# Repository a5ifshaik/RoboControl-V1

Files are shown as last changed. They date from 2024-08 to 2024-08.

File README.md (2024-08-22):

# RoboControl V1 - Arduino-based Robot Control Board
<p align="justify"> The RoboControl is a cheap and beginner-friendly all-in-one robot control board which is capable of dual motor control (6A/Channel), and includes dedicated pinouts for servos, sensors and external 12V systems which is controlled using a MOSFET. It also features a built in battery level sensing circuit which is made up of a simple voltage divider that translates the 0-12V range of the input battery to a analog value range between 0-1023. </p>



## Features
- 12V - 24V Input Voltage
- Arduino Nano MCU
- Two Infineon IFX9201SG Motor Drivers (Supports up to 6A/driver)
- MOSFET for External Circuit Control
- Battery Voltage Monitor
- Dedicated ports for sensors/servos

## Pinout 
| On RCB | Arduino Pin | Description | 
| --- | --- |  --- |
| S1 | D6 | Servo 1 Port; comes with 5V and GND supply |
| S2 | D9 | Servo 2 Port; comes with 5V and GND supply |
| SCL | A5 | Serial Clock Line used for I2C | 
| SDA | A4 | Serial Data Line used for I2C | 
| BZOUT | D7 | MOSFET control line, 5V to turn on 12V line |
| TRIG | D12 | Trigger Pin for Ultrasonic Sensor (Can use as normal digital)  |
| ECHO | D11 | Echo Pin for Ultrasonic Sensor (Can use as normal digital) |
| BATT | A3 | Battery monitor pin, produces analog reading between 0 - 1023  |
| M1 PWM | D3 | PWM Signal supply pin for Motor 1 driver |
| M1 DIR | D8 | Motor 1 Direction Pin (1/0 for CW/CCW or vv) |
| M1 EN | D2 | Motor 1 Enable Pin, Set as HIGH to enable driver |
| M2 PWM | D5 | PWM Signal supply pin for Motor 2 driver |
| M2 DIR | D10 | Motor 2 Direction Pin (1/0 for CW/CCW or vv) |
| M2 EN | D4 | Motor 2 Enable Pin, Set as HIGH to enable driver |

## Schematics:


## 3D Render


## Sample Applications
### The RoboControl board was initially developed for a home-surveillance robot with 2 wheels, but can be used for various applications that have similar needs.



###### **In Image 2, the yellow jumpers are used to correct an error found post-production which has since been rectified in this repository.

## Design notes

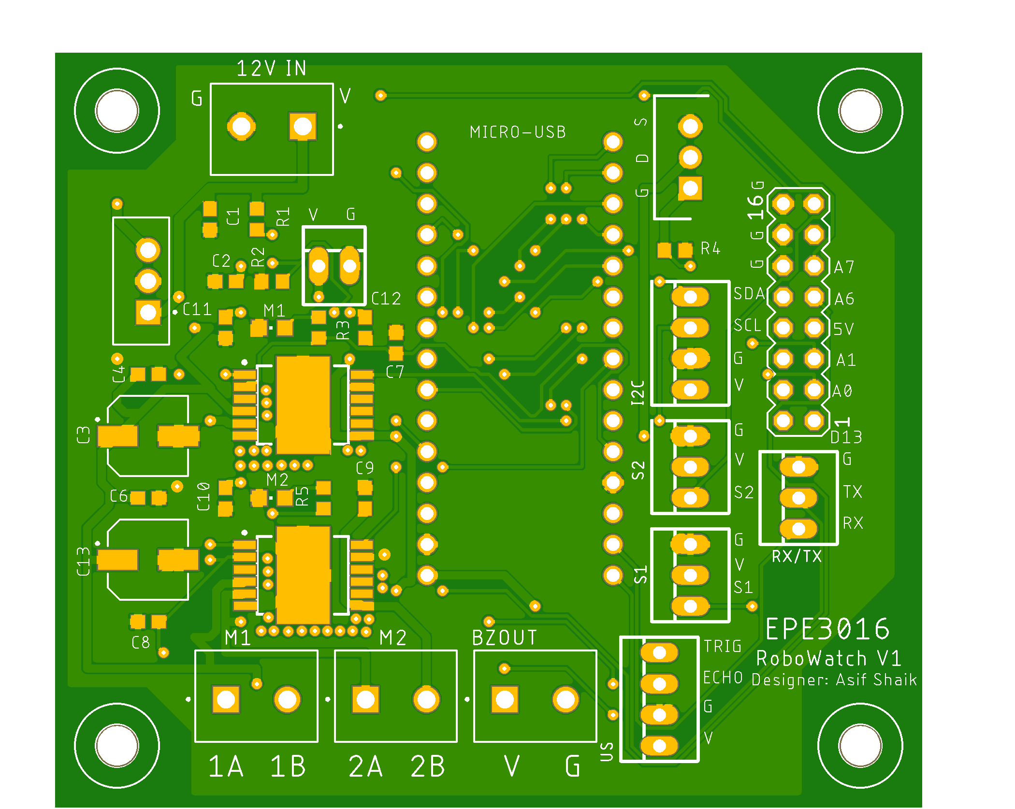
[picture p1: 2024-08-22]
3D Board Render.png

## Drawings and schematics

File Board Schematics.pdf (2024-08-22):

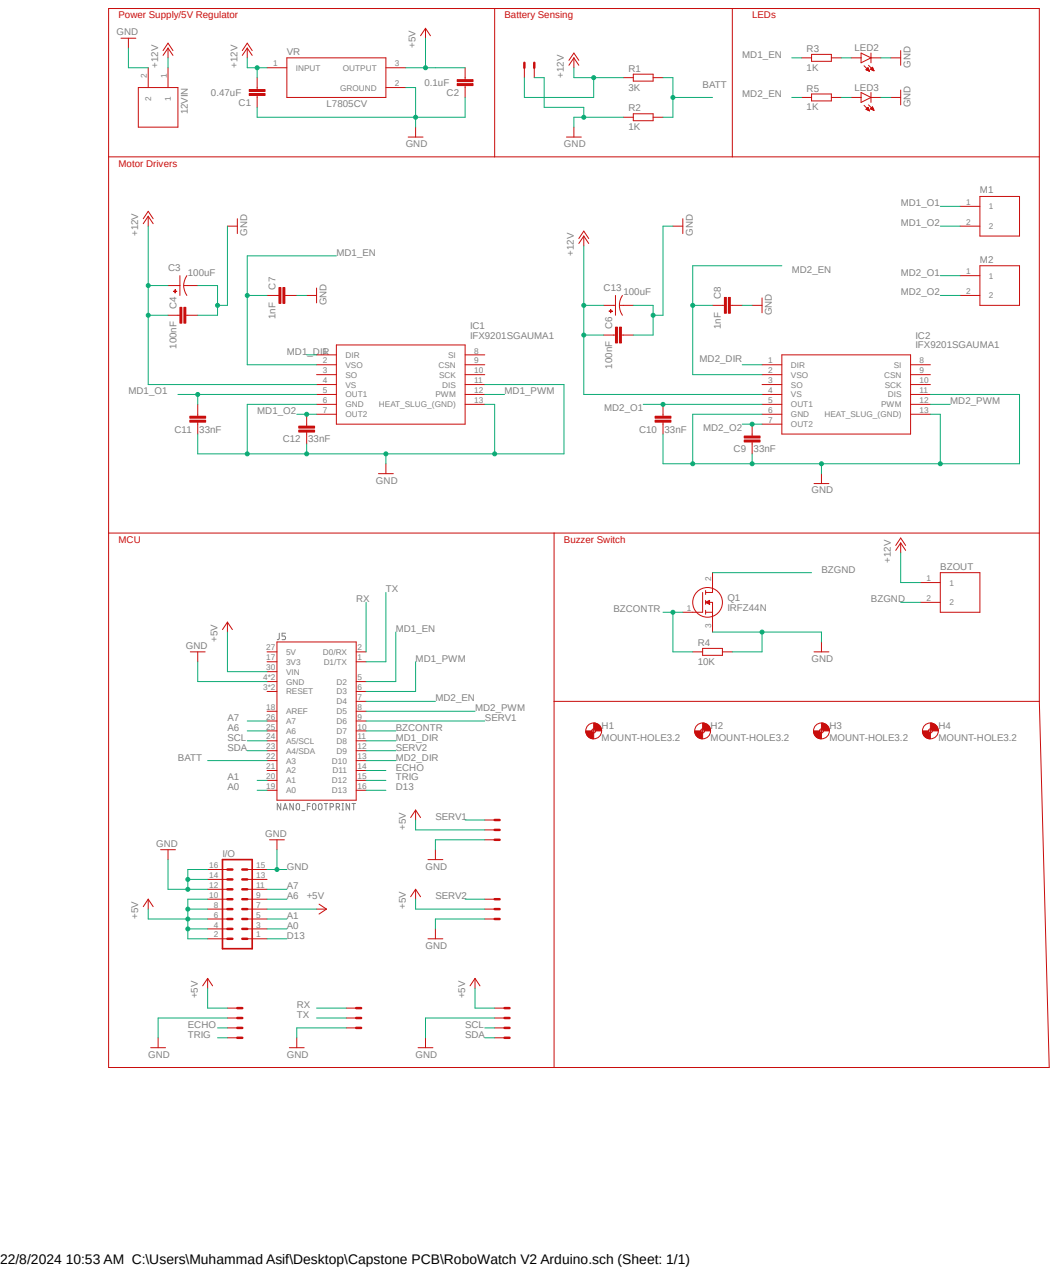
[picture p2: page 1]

6 | 5 TX

22/8/2024 10:53 AM C:\Users\Muhammad Asif\Desktop\Capstone PCB\RoboWatch V2 Arduino.sch (Sheet: 1/1)

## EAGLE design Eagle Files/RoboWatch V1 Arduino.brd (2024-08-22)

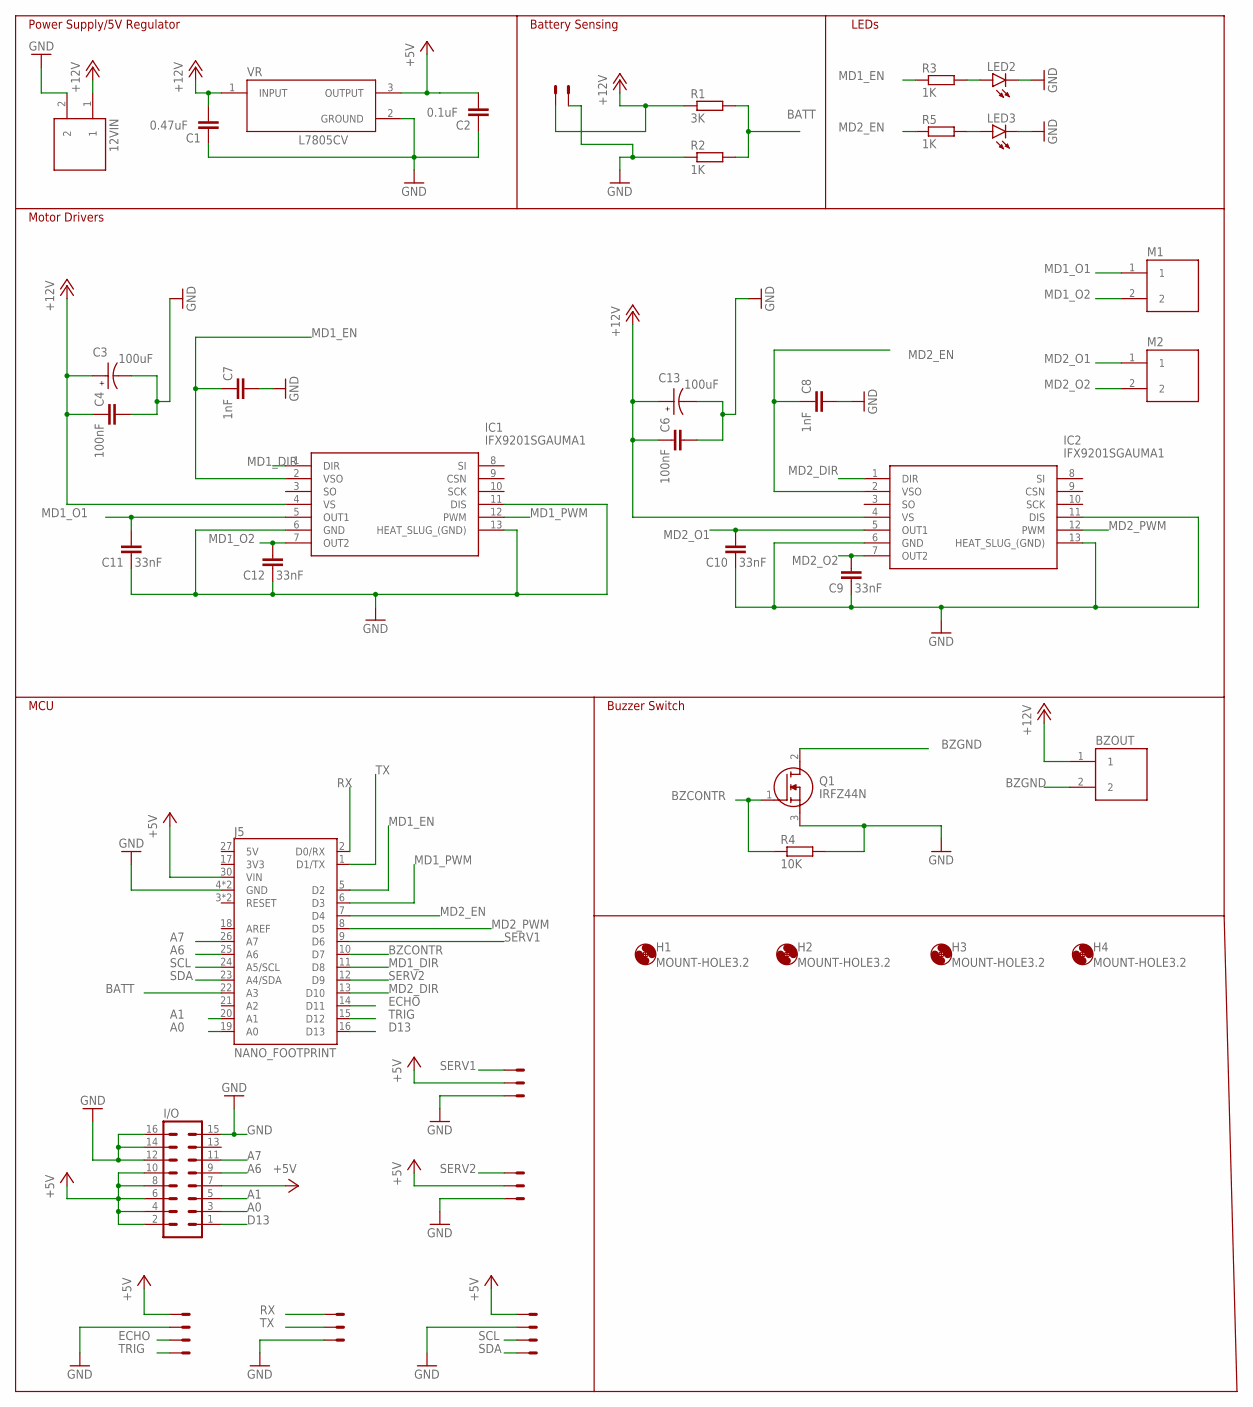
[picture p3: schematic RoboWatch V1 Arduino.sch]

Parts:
12VIN: KF301-2P; HANDSON_KF301-2P
BZOUT: KF301-2P; HANDSON_KF301-2P
C1: 0.47uF; C0603
C2: 0.1uF; C0603
C3, C13: 100uF; CAP_EEEFN1E101UP
C4, C6: 100nF; C0603
C7, C8: 1nF; C0603
C9, C10, C11, C12: 33nF; C0603
H1, H2, H3, H4: MOUNT-HOLE3.2; 3,2
I2C: 22-23-2041
I/O: MA08-2
IC1, IC2: IFX9201SGAUMA1; PG-DSO-12-17
J5: NANO_FOOTPRINT; NANO
LED2, LED3: LEDCHIPLED_0805; CHIPLED_0805
M1, M2: KF301-2P; HANDSON_KF301-2P
Q1: IRFZ44N; TO254P440X1000X1900-3P
R1: 3K; R0603
R2, R3, R5: 1K; R0603
R4: 10K; R0603
RX/TX: 22-23-2031
S1, S2: 22-23-2031
US: 22-23-2041
VR: L7805CV; TO255P1040X460X1968-3
X4: 22-23-2021

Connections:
+5V: C2.2, I2C.1, I/O.2, I/O.4, I/O.6, I/O.7, I/O.8, I/O.10, J5.30 (VIN), S1.2, S2.2, US.1, VR.3 (OUTPUT)
+12V: 12VIN.1, BZOUT.1, C1.2, C3.1, C4.1, C6.1, C13.1, IC1.4 (VS), IC2.4 (VS), R1.1, VR.1 (INPUT), X4.1
A0: I/O.3, J5.19 (A0)
A1: I/O.5, J5.20 (A1)
A6: I/O.9, J5.25 (A6)
A7: I/O.11, J5.26 (A7)
BATT: J5.22 (A3), R1.2, R2.2
BZCONTR: J5.10 (D7), Q1.1 (G), R4.1
BZGND: BZOUT.2, Q1.2 (D)
D13: I/O.1, J5.16 (D13)
ECHO: J5.14 (D11), US.3
GND: 12VIN.2, C1.1, C2.1, C3.2, C4.2, C6.2, C7.2, C8.2, C9.1, C10.1, C11.1, C12.1, C13.2, I2C.2, I/O.12, I/O.14, I/O.15, I/O.16, IC1.6 (GND), IC1.11 (DIS), IC1.13 (HEAT_SLUG_(GND)), IC2.6 (GND), IC2.11 (DIS), IC2.13 (HEAT_SLUG_(GND)), J5.4 (GND), J5.29 (GND), LED2.C, LED3.C, Q1.3 (S), R2.1, R4.2, RX/TX.3, S1.3, S2.3, US.2, VR.2 (GROUND), X4.2
MD1_DIR: IC1.1 (DIR), J5.11 (D8)
MD1_EN: C7.1, IC1.2 (VSO), J5.5 (D2), R3.1
MD1_O1: C11.2, IC1.5 (OUT1), M1.1
MD1_O2: C12.2, IC1.7 (OUT2), M1.2
MD1_PWM: IC1.12 (PWM), J5.6 (D3)
MD2_DIR: IC2.1 (DIR), J5.13 (D10)
MD2_EN: C8.1, IC2.2 (VSO), J5.7 (D4), R5.1
MD2_O1: C10.2, IC2.5 (OUT1), M2.1
MD2_O2: C9.2, IC2.7 (OUT2), M2.2
MD2_PWM: IC2.12 (PWM), J5.8 (D5)
unnamed: LED2.A, R3.2
unnamed: LED3.A, R5.2
RX: J5.2 (D0/RX), RX/TX.1
SCL: I2C.3, J5.24 (A5/SCL)
SDA: I2C.4, J5.23 (A4/SDA)
SERV1: J5.9 (D6), S1.1
SERV2: J5.12 (D9), S2.1
TRIG: J5.15 (D12), US.4
TX: J5.1 (D1/TX), RX/TX.2

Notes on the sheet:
Power Supply/5V Regulator
Motor Drivers
MCU
Battery Sensing
LEDs
Buzzer Switch

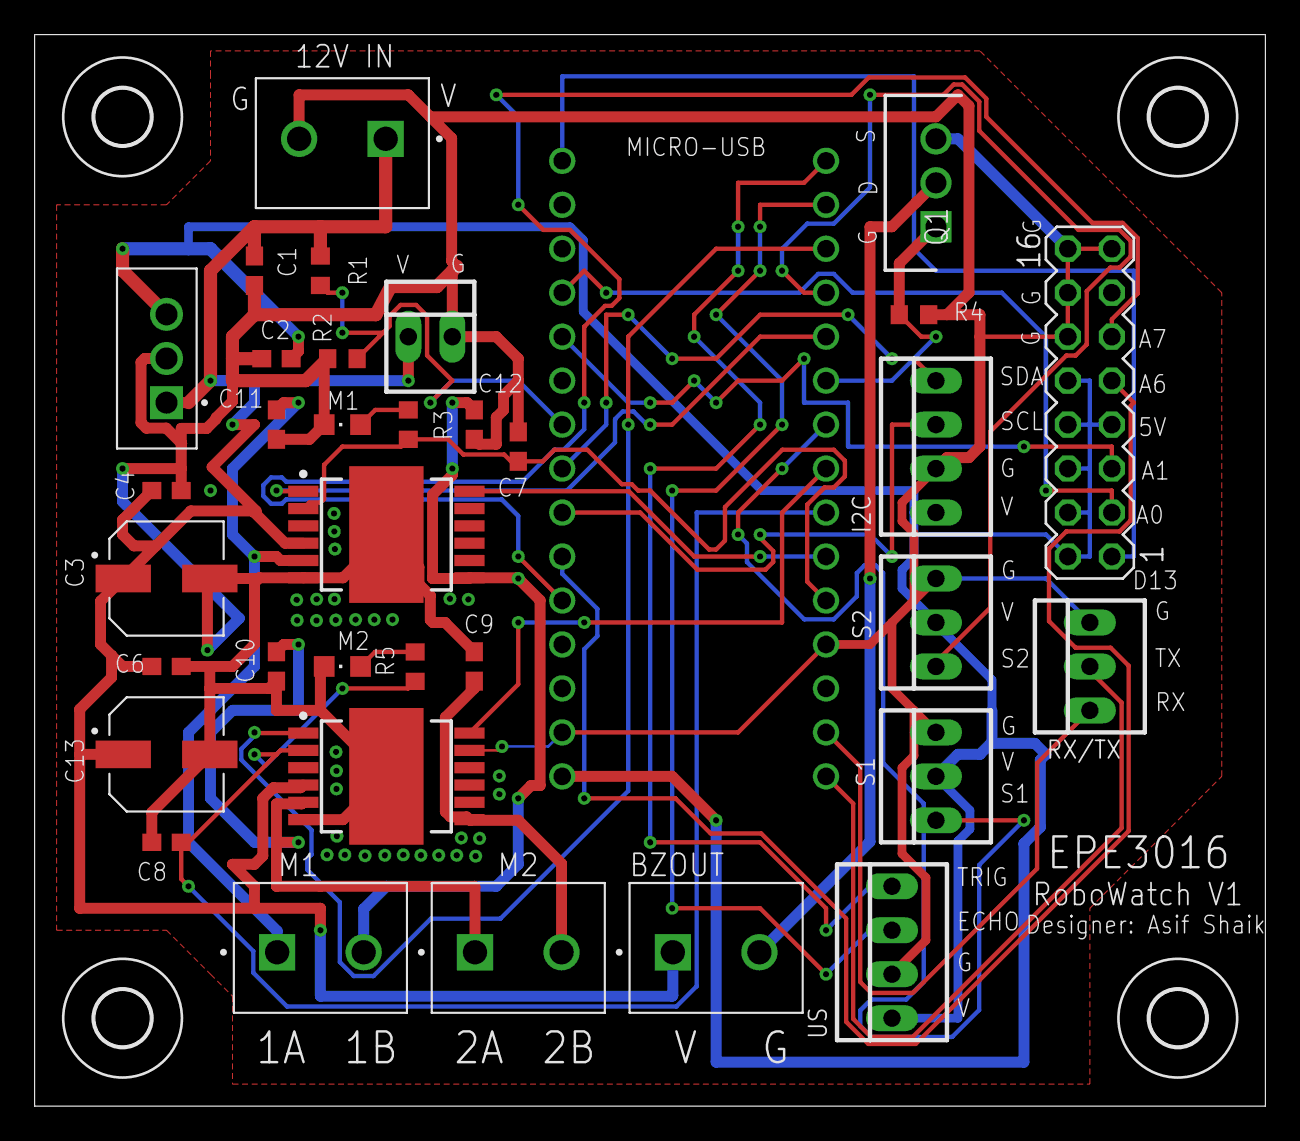
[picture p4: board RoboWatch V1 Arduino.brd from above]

Board: 2 copper layers, 71.1 x 61.9 mm, 39 parts (0 on the bottom side), 31 nets.

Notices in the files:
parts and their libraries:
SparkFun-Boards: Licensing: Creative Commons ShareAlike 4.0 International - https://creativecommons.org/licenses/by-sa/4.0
